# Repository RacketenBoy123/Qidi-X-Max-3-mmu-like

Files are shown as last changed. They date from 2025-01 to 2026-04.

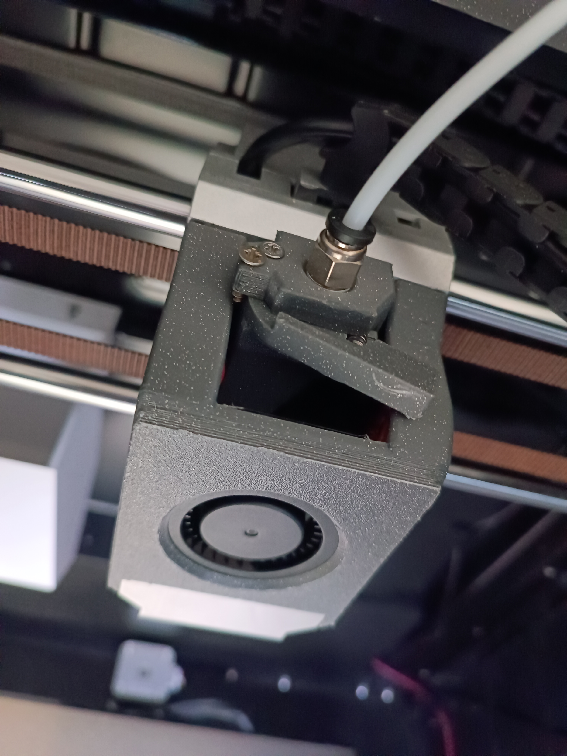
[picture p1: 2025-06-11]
assets/images/Printhead_1.jpg

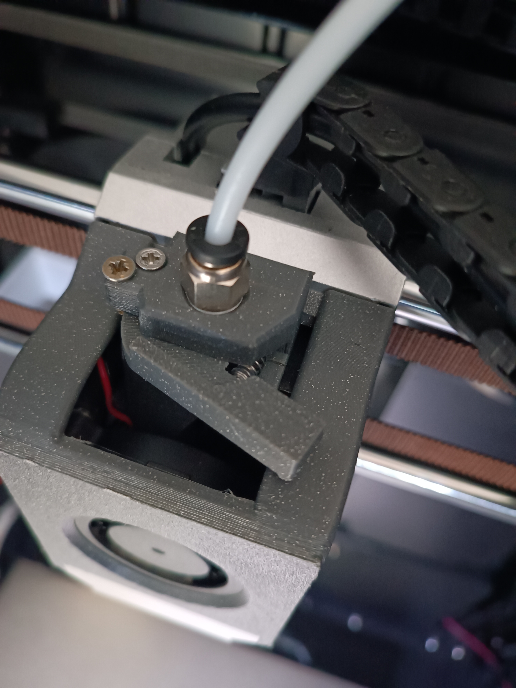
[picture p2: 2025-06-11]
assets/images/Printhead_2.jpg

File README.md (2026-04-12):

# Qidi-X-Max-3 mmu-like BRANCHHHH
 A fan-made MMU/AMS-like system for the Qidi X Max 3
 It is fully created in G-code and uses the FreeDi replacement system for the Qidi printer as a base. For instructions on how to install FreeDi, go here: : [FreeDi](https://github.com/Phil1988/FreeDi/tree/master)

 I also recommend that you upgrade the internal eMMC module to a 32GB one.

# Hardware needed
As of the hardware side you only need:

1. 1 x Bigtreetech SKR Pico
2. 1 to 4 Nema 17 (E series) Motors (Recommended: [Nema 17 Motors](https://www.amazon.de/dp/B0B93PNYCP?ref=ppx_yo2ov_dt_b_fed_asin_title)) and 1 to 4 longer dupont cables 
3. 1 to 4 Extruders with mounting hardware (Recommended: [Dual drive extruder](https://www.amazon.de/dp/B0865SLWQ5?ref=ppx_yo2ov_dt_b_fed_asin_title))
4. PTFE Tubing and fittings (Recommended: [5m PTFE tuning and fittings](https://www.amazon.de/FULARR%C2%AE-Professionell-Teflonrohr-Fitting-Verbinder/dp/B07R9JXQF4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))
5. 16 M3 Heated inserts and 16 M3x7mm screws
6. 1x 5 to 5.5mm diameter spring

Optional:

7. 1 x Ikea Samla 22L box [Link](https://www.ikea.com/de/de/p/samla-box-mit-deckel-transparent-s69440822/#content)
8. Sealing for the Samla box
9. 1 x PVC Pipe, 33mm or 40mm diamater and 32cm length
10. 1 x Hygrometer
11. Silicat

# Disclaimer
Before you print or install anything, be sure to install FreeDi and the matching version of Klipper on your SKR Pico. After that, you can proceed.
A disclaimer before you start: the AMS riser, toolhead, filament cutter, Samla box filament holder, and nozzle wiper are all from different creators. Most of these files I edited and changed to make them work better, but please still support the original creators. All of the original links are in the folders as a text file or in this installation guide. Thanks.
If anthing doesnt work for you or theres a bug in the gcode, please contact me.

# Installation
The first step is printing the needed adapters and hardware. I recommend printing these parts all in either ABS or ASA to make them more heat resistant.
If you don’t know how to proceed at any step, please look at the included pictures or message me. Included pictures are in the /assets/images folder and named after what they might help with assembling. 
Go through the stl_files folder and download the following STL files and print them the amount stated below:

### Ams Riser

1. 1x 4-way_splitter-flat.stl
2. 1x xmax-mmu-lf.stl
3. 1x xmax-mmu-lr.stl
4. 1x xmax-mmu-rf.stl
5. 1x xmax-mmu-rr.stl
6. 8x mmu-xmax_joiner-clip-x8-v1.stl

After printing the needed hardware for the riser, go through the "732980-x-max-3-automatic-multi-material-riser-ec3e07c0-a392-4935-88c6-fceb8f445ebd.pdf" or click this [Link](https://www.printables.com/model/732980-x-max-3-automatic-multi-material-riser/files) to see how to assemble the printed pieces. For that, push the heat-set inserts into the designed holes on the side of the riser pieces with a soldering iron.

### MCU Holder

1. 1x Back_Spool_Holder_Adapter.stl
2. 1x MCU_Holder v2.stl
3. 1x ams_cover.stl (Optional)

Detach the spool holder from the backside of the printer.
Then take the "Back_Spool_Holder_Adapter.stl" and the "MCU_Holder v2.stl" and screw them together. Now place the MCU over the screw holes of the holder, with the heat-set inserts, and screw the SKR Pico onto the holder.
Now place the adapter in the slot that is now free at the back of the printer and slide it down.
Before this step, be sure to power off the printer. Now you just need to open the back plate of the printer, take a USB cable, attach it to the mainboard of the printer, fish it through the vent cutouts, and plug it into the SKR Pico.
After that, make sure to close everything back up, power on the printer, and configure the SKR Pico via SSH [Tutorial](https://www.youtube.com/watch?v=hfD1LAOoBJc).

### Toolhead

This segment contains a replacement for the toolhead cover, to make it more accessible, and a filament cutter that replaces the stock filament guide and adds a place for a knife blade. The STL files also contain a "Cutter_Stop.stl", which is a plug to push into one of the holes in the front of the chassis, which, when equipped with a heat-set insert and a screw, will push the filament cutter in and cut the filament when needed.

1. 1x Cutter_Stop.stl
2. 1x Filament_cutter.stl
3. 1x Filament_cutter_arm.stl

Optional:

4. 1x qidi_front_adapter_short.stl
5. 1x Qidi_front_cover v2.stl
6. You also need magnets with a 10mm daimeter

After printing these parts, unload the filament out of the printhead, power off the printer, and take off the front cover of the toolhead. Take out the original PTFE tube and the original fitting.
Before you now place in the replacement, make sure to screw in one of the fittings (the silver one) into the big hole at the top. I recommend using a bit of heat from a heat gun to preheat the hole so the printed part won’t snap in two.
Now place the "Filament_cutter.stl" onto the printhead; the square pillar should align with the square cutout right beneath the filament inlet.
After that, take the "Filament_cutter_arm.stl", place a small knife blade into the slot on the side, with the hole at one end facing up. After that, take the arm and align the hole at one end with the further back hole of the "Filament_cutter.stl" and put a screw through both of these. Now take the spring and place it on the sideways hole on the "Filament_cutter.stl", the small hole that doesn’t go through and points towards the "Filament_cutter_arm.stl". After that, take another screw and place it in the other hole on the "Filament_cutter.stl" as a stop for the "Filament_cutter_arm.stl" so it doesn’t open too wide.

Printhead_2

At the end put a heat-set insert in the  "Cutter_Stop.stl", put a screw in the insert and let it stick out about 25mm and then push the block in the square hole at the end of the light strip, with the srew further to the top.

Stop_1

After that, you can optionally install the magnetic printhead cover. For that, follow this [Link](https://www.printables.com/model/952804-filament-cutter-for-x-plussmartmax-3-toolhead).

### Poop Bucket

1. 1x Bucket_Filament.stl

Bucket_3

To install this, slide it into the flat steel at the back of the printer (internally) and follow the included pictures.

### Nozzle Wiper

1. 1x Wipe_arm.stl
2. 1x Wipe_clamp.stl

Wiper_1

Follow the included pictures and this [Link](https://www.printables.com/model/722217-qidi-x-max-3-nozzle-scrub-holder)

### Filament Storage

1. 2x Ikea_box_holder.stl
2. 1x to 4x angled_feeder_outside_m6_for_greater_gap.stl

Optional:

3. 2x PVC_Adapter.stl (Optional)
4. 3x Spool Trenner.stl (Optional for 33mm diameter PVC Pipe only)
5. samla_clips.stl (Optional)

Samla_1

Follow this [Link](https://www.thingiverse.com/thing:1752874)

Carto mount: PC
Rest: abs

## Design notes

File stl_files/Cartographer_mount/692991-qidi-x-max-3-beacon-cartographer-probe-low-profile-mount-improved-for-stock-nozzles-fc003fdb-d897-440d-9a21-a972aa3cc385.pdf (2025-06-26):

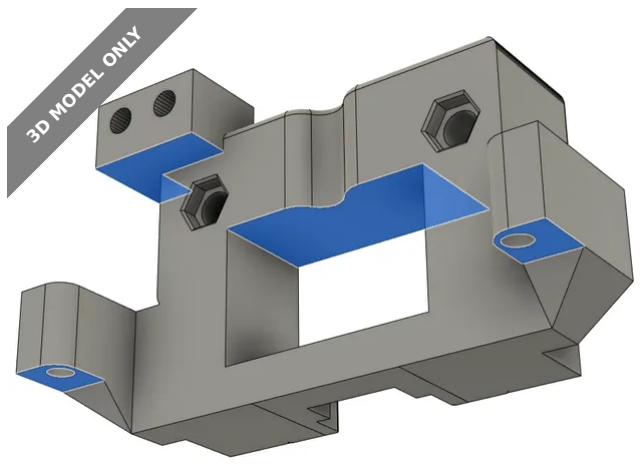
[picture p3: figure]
3D MODEL ONLY

## Summary

QIDI X-Max 3 Beacon / Cartographer low-profile mount for stock nozzle setup

3D Printers (https://printables.com/model?categoryId=1) > Other Printer Parts & Upgrades (https://printables.com/model?categoryId=2)

Tags: | qidi | beacon | qidixmax3 | cartographer

Thnx for @Balgerion for original model!

Update:

Version 2 of mount makes it 1mm lower, for better auto Z calibrations. It does require low-profile button head screws, regular DIN 912 cap head screws won't work. They have too big head

This is slightly improved remix, adding some quality of life features and third leg for stock nozzle setup
If you need X-Plus 3 version, there are some remixes for it
Supported probes:

Mc Sneaky (https://printables.com/@McSneaky_1598019)

## QIDI X-Max 3 Beacon / Cartographer probe (low profile) mount improved for stock nozzles

VIEW IN BROWSER (https://printables.com/model/692991-qidi-x-max-3-beacon-cartographer-probe-low-profile)

updated 23. 11. 2024 | published 23. 11. 2024

This mount works with both Beacon D (https://beacon3d.com/product/beacon/) low profile version and Cartographer (https://cartographer3d.com/) low profile (that's what I'm using)
Needed hardware:
4x M3x14 bolts original stock probe mount bolts. Stock probe has 2 bolts, there should be 2 extra that came with printer / official upgrade package as spare parts
2x M3 nuts to secure probe in place. Those didn't come with printer, had to buy
2x M2.5x16 had those with one of Qidi printers as spare parts too, can't remember if it was iFast or X-Max 3
Optional zipties to secure cable
Print settings:
Print in some high-temp material. PLA will warp most likely, ABS and ASA MIGHT survive. I'd recommend PAHT-CF rated for 190deg C, PP-GF30 or PSU to be sure it doesn't warp nor melt. Did in PAHT-CF myself
I did with 4 walls, 4 top layers, 4 bottom layers, 50% infill
Need supports in two areas marked as blue on model picture After-installation needed config changes Cartographer:

Install Carto in Klipper: Carto install docs (https://docs.cartographer3d.com/installation-and-setup/klipper-setup)

Modify printer.conf

Comment out / remove whole [homing_override] section
Under [bed_mesh]
mesh_min:25,25 # this needs to be set to 25,25 from stock 25,15 speed:500 # increase speed for faster scanning, can leave stock probe_count:30,30 # increase points count, can leave stock
Add [cartographer] and [safe_z_home] sections following to their doc (https://docs.cartographer3d.com/installation-and-setup/klipper-config)
under [cartographer] need to set y_offset: 25
under [safe_z_home] need to set home_xy_position: 162.5, 162.5
Remove / comment out any [probe] and [bltouch] sections Follow Carto docs (https://docs.cartographer3d.com/installation-and-setup/cartographer-calibration) for initial calibration. It's super easy, just 2-3 steps

Running full bed mesh at 300mm/s. Printer should also be able to handle 600mm/s

Beacon:
- Don't know. Ask @Balgerion =)

## This remix is based on

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
## Model files

QIDI X Smart/Plus/Max Beacon probe (low profile) mount (https://printables.com/model/639766-qidi-x-smartplusmax-beacon-probe-low-profile-mount)
by Balgerion (https://printables.com/@Balgerion_812626)

## License

This work is licensed under a GNU

General Public License v2.0 (http://www.gnu.org/licenses/old-licenses/gpl-2.0.html)

✖ | Sharing without ATTRIBUTION
✔ | Remix Culture allowed
✔ | Commercial Use
✔ | Meets Open Definition

qidi_beacon_mount.stl

qidi_beacon_mount.obj

qidi_beacon_mount.step

beacon_carto_mount_v2.stp

beacon_carto_mount_v2.stl ℹ | Share under the same license

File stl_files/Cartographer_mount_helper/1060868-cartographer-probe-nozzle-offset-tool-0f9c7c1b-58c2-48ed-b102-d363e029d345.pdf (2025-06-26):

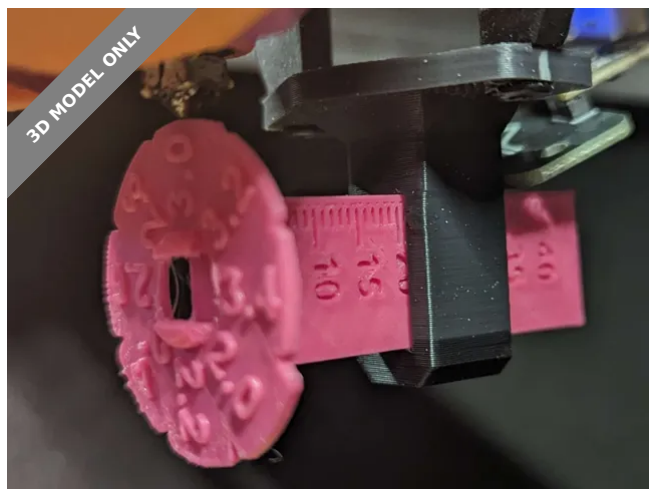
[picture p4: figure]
3D MODEL ONLY

## Summary

A simple tool to help find the Z and Y offset for your Cartographer probe.

3D Printers (https://printables.com/model?categoryId=1) > Other Printer Parts & Upgrades (https://printables.com/model?categoryId=2)

Tags: cartographer

This simple tool helps find the proper offset for your Cartographer probe in relation to your nozzle tip.
Having a 2.6-3mm Z offset is critical for reliable operation of Cartographer Touch (nozzle probling).
The Y offset ruler is just a helpful addition.
To use, simply print the parts (they are already in proper printing orientation in the .3mf file) and then clip the “flower” onto the “ruler” then slide the “ruler” into the base.
Then simply remove your cartographer from your mount and replace it with the tool. Slide the ruler until the flower is underneath the nozzle, then rotate the flower until one of the faces is touching the nozzle.
The numbers on the flower indicate your Z offset, and the ruler mark that lines up with the base indicates your Y offset (you can also use calipers to measure from the back face of the flower to the front face of the base and this will also be your Y offset).

E (https://printables.com/@Esoterical_306854) Esoterical (https://printables.com/@Esoterical_306854)

## Cartographer probe nozzle offset tool

VIEW IN BROWSER (https://printables.com/model/1060868-cartographer-probe-nozzle-offset-tool)

updated 20. 11. 2024 | published 20. 11. 2024

## Model files

## License

This work is licensed under a GNU

General Public License v3.0 (https://www.gnu.org/licenses/gpl-3.0.html)

✖ | Sharing without ATTRIBUTION
✔ | Remix Culture allowed
✔ | Commercial Use
✔ | Meets Open Definition
ℹ | Share under the same license carto_nozzle_offset_tool.3mf

carto_nozzle_offset_tool.step

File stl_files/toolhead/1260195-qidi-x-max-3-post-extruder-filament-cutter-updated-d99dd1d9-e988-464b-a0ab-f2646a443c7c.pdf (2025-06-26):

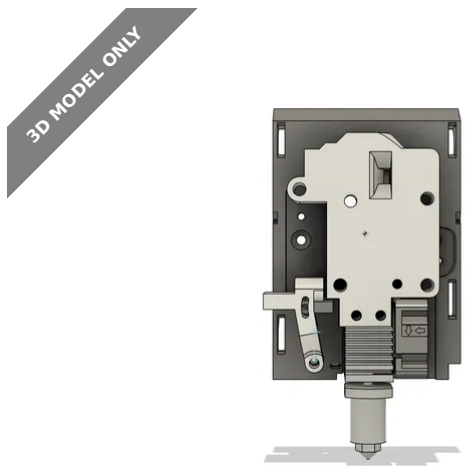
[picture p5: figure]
3D MODEL ONLY

## Summary

QIDI X-Max 3 extruder with ECAS fitting and runout sensor and extruder disengage slot.

3D Printers (https://printables.com/model?categoryId=1) > Other Printer Parts & Upgrades (https://printables.com/model?categoryId=2)

Tags: | extruder | filamentcutter | qidi | qidixmax3

I believe I have a working Beta

Updated: (4/22/2025)

https://vimeo.com/manage/videos/1077693101/502d7b66e4

This is a work in progress! Proceed with caution.

Additionally, this will also require a new homing procedure.

The goal of this project is to add a sturdy and integrated filament cutter that minimizes waste while keeping the rest of the printer as stock as possible.

AskewedBox (https://printables.com/@AskewedBox_2060075)

## QIDI X-Max 3 (Post Extruder) Filament cutter (Updated)

VIEW IN BROWSER (https://printables.com/model/1260195-qidi-x-max-3-post-extruder-filament-cutter-updated)

updated 22. 4. 2025 | published 22. 4. 2025

This design is a modified version of the original extruder body. It includes a filament cutter "blade port" positioned directly above the hotend and has been simplified for easier printing.

Side note: QIDI originally had a design for this but not on the release model I have.

In addition to the filament cutter, this modification incorporates a filament runout sensor placed above the extruder. The runout sensor utilizes a 5 mm bearing (original this was a 4.5mm BB) and an Omron D2F style limit switch: https://www.digikey.com/en/products/detail/omron-electronics-inc-emc-div/D2F/83270 (https://www.digikey.com/en/products/detail/omron-electronics-inc-emc-div/D2F/83270)
Required:

Printed Parts

Extruder Cover (Front (no supports needed), Left Panel, Right Panel) Lever Arm
Lever Arm Spacer
Blade Holder (print a few)
Notes
I printed in ABS with 40% infill and 4 walls.
The Left and Right Panels as well as the lever arm need support everything else should be fine.
I was having issues with the tabs snapping no matter how I printed them so I broke it up into multiple parts them printed for strength. As a plus this makes it easier to transfer the extruder fan.

Filament Sensor

1x 5mm Bearing
1x Omron D2F style limit switch
2x Self-tapping M2x8mm screws
Optional but helpful: long M2 screws to adjust the limit switch

Extruder

ECAS04
4x M3 heat set inserts of any length for the extruder body
2x M3x4 heat set inserts for the hotend mount holes
2x M3 heat set inserts of any length for the cover if you print this in multiple pieces.

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
Cutter

18mm Snap-off Blade with 8mm segments - I bought mine at Harbor Freight.
1x M3X20 screw
4 mm OD, 0.5mm Wire Size, 15 mm compression spring - It is important that these are stiff, I got mine from my Box Turtle Kit These should work but are untested https://www.amazon.com/gp/product/B0C33BYX83/ (https://www.amazon.com/gp/product/B0C33BYX83/)
Superglue
Instructions (in work):

Extruder

Insert the ECAS fitting (this should be hard to insert, I pressed it in using a vise)
Filament Sensor
Insert the 5mm bearing ensuring that it moves freely.
Insert the limit switch in the correct orientation
Insert the optional M2 screws to apply pressure light pressure to the switch.
To adjust the placement of the switch take a piece of filament and insert it in the extruder listening for a click as you insert it. If you don't hear a click tighten the M2 screws and try again.
It is critical that you ensure that the switch is triggered by the filament before setting its placement permanently. Use the Self-tapping M2 screws set the switch location. Transfer the extruder hardware from the stock extruder. Be careful not to lose the tension spring or the gear bearings. The print is designed without tolerances for the bearings or gear pins, so some hardware mainly the dowel pins, may be difficult to insert.
I pressed in the bearing and reamed the dowel hole with a 3mm bit.
This will still be tight fit but easer to remove if needed. Insert 4 M3 heat-set inserts into the extruder body flush.
For the hotend, ensure the inserts are 4mm or less. Reassemble the extruders gears and reattach the back plate Check that the gears turn freely
Notes
Don't attach the hotend yet; you will want it off to verify blade length and smooth movement.
Ensure that no plastic is displaced that will cause the blade to bind.

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
The have been increased to 4.2 mm but might still be slightly undersized
Ensure the tenson spring is not binding on the plastic was displaced by the insert.

Blade Holder

-----Use Caution when handling and snaping the blades!

The holder is designed for a 8mm wide section from a snap-off box cutter blade
The blade needs to be snapped to a length of of approximately ~18mm (measures from the cutting edge) or slightly less. Insert the blade into the holder such that the lever assembly is around 25.7mm (This is what worked for me through guess and check)
Glue the blade into the holder.
Now is a good time to check that the blade is free moving in the extruder blade slot and that it extends past the filament hole by at least 1mm.
Note
I used a vise and pliers to snap this to make clean(er) breaks but even then it wasn't consistent.
The goal is to have a blade length that is long enough to cut the filament but isn't so long that it binds when retracted by the spring.
It is hard to snap this exactly and this might take a few tries.
This section will probably require trial and error.
The lever arm length and hole depth were fiddly to get just right and may require adjusting to get the correct blade length.

Lever Arm

Screw the assembled holder into the lever with two short M2 screws, Don't over tighten these since they should be free moving. Insert the M3x20 mm screw into the lever arm (these should be relatively free moving on the screw.
Insert the screw into the printed spacer.
Screw the lever are onto the preexisting hole with a threaded insert next to the hotend

____________________________________________

Untested Best Guess at Hotend Values BoxTurtle MMU:

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
## Model files

tool_stn: 44.5
tool_stn_unload: 96.6
variable_retract_length: 23.7 variable_pushback_length: .9 (most likely wrong)

## This remix is based on

GitHub - vega-d/qidi_mods: a set of mods to qidi printers. Assorted by model. (https://github.com/vega-d/qidi_mods)

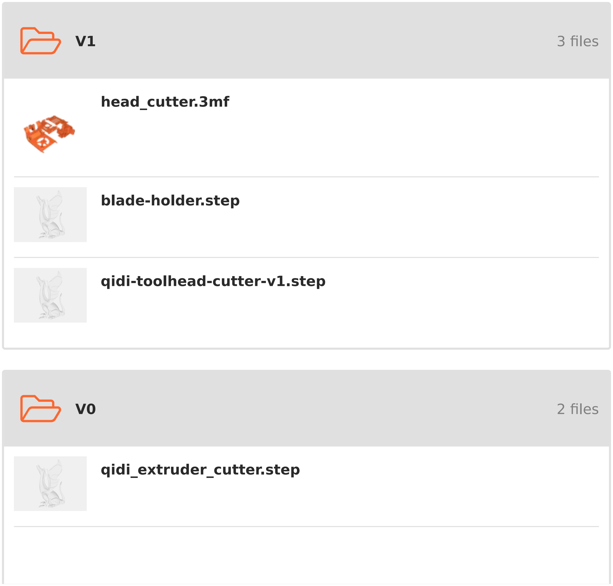
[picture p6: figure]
3 files; 2 files; head_cutter.3mf; blade-holder.step; qidi-toolhead-cutter-v1.step; qidi_extruder_cutter.step

## License

This work is licensed under a
Creative Commons (4.0 International License)

Attribution (http://creativecommons.org/licenses/by/4.0/)

✖ | Sharing without ATTRIBUTION
✔ | Remix Culture allowed
✔ | Commercial Use
✔ | Free Cultural Works
✔ | Meets Open Definition

qidi_extruder_assembly.step

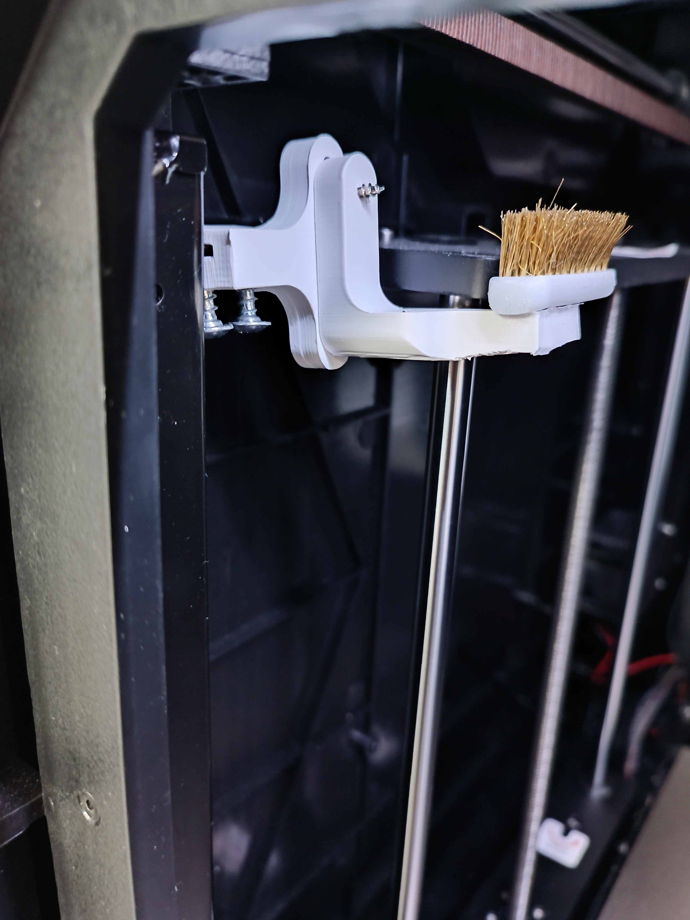
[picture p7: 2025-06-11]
assets/images/Wiper_1.jpg

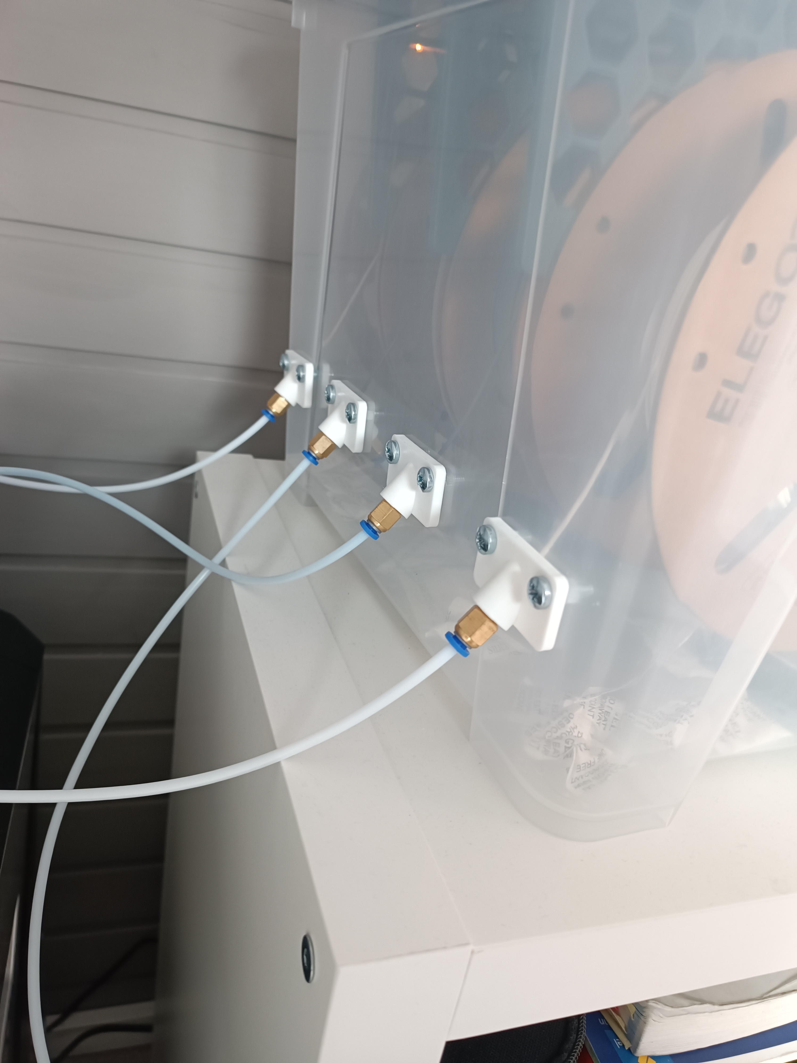
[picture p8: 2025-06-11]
assets/images/Samla_1.jpg

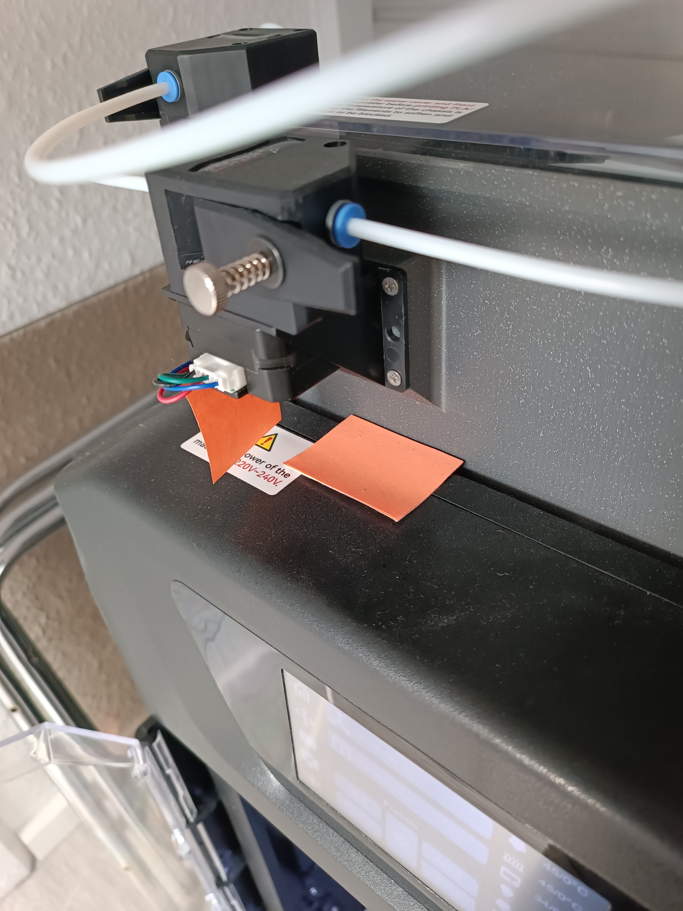
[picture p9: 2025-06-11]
assets/images/Riser_2.jpg

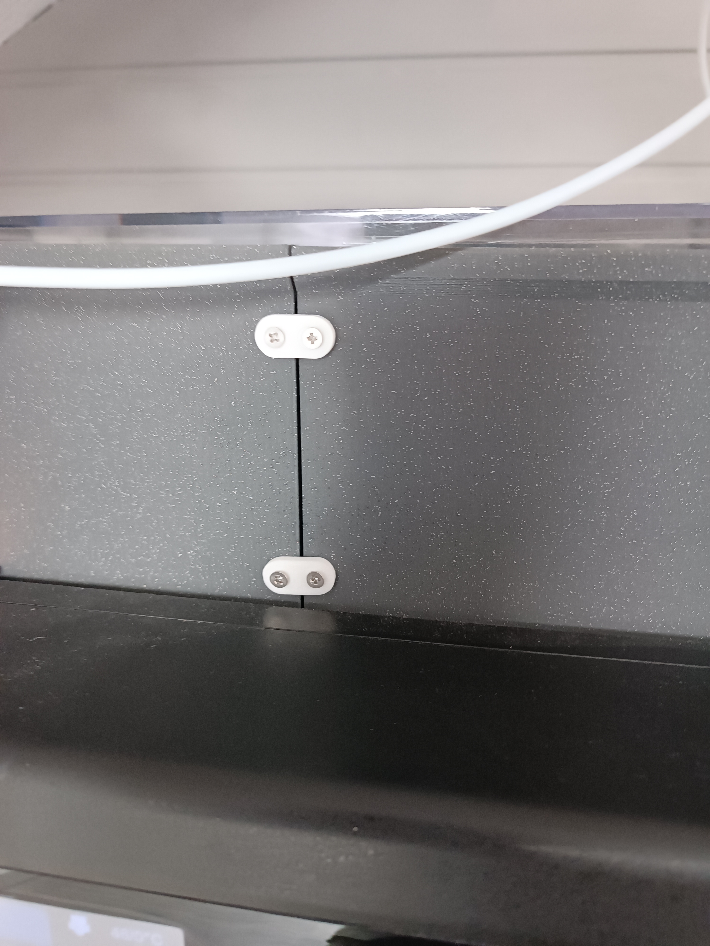
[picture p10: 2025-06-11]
assets/images/Riser_3.jpg

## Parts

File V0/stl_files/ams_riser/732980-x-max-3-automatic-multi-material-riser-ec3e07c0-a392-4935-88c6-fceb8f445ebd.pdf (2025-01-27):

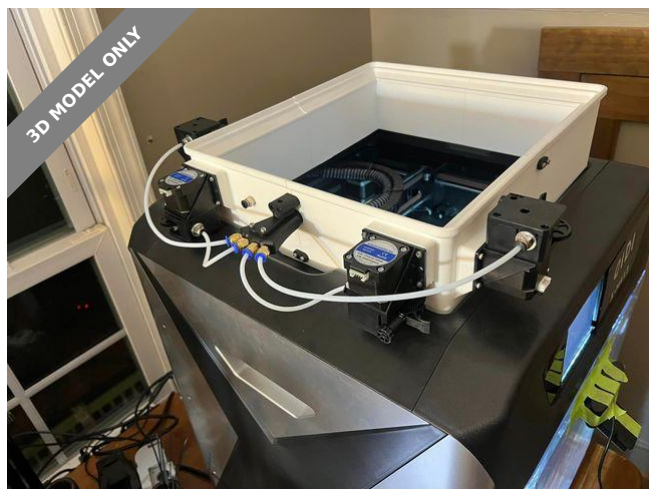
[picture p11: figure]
3D MODEL ONLY

## Summary

Multi material and color

3D Printers (https://printables.com/model?categoryId=1) > Other Printer Parts & Upgrades (https://printables.com/model?categoryId=2)

Tags: mmu | qidi | ams | xmax3

this is for the qidi x max 3.

its a riser in 4 pieces meant to house a splitter a pc4 m10 coupler and up to 8 titan extruders acting as feeder extruders to be synced with your DD extruder.

you will need either a board upgrade with more stepper drivers or an expansion board. im using a BTT Octopus v1.1

i use the Jazz3D Spit Fire print head with the filament cutter to make color/ material changes seemless. which uses the orbiter v2 and a rapido uhf.

recommend printing in petg or abs very minimal support roughly 1.5kg in filament depending on your print settings.

i provided the dxf if youd like to get a poly carbonate top made

you will need pc4 6mm couplings and drill the brass out with 4mm drill bit for smooth transition to the splitter and the pc4 10mm once Bowden is

z (https://printables.com/@zfriedman302_262860) zfriedman302 (https://printables.com/@zfriedman302_262860)

## X Max 3 Automatic

## Multi Material Riser

VIEW IN BROWSER (https://printables.com/model/732980-x-max-3-automatic-multi-material-riser)

updated 3. 3. 2024 | published 3. 3. 2024

## Model files

pushed thru you need to flare the ptfe I used a drill with a #2 Phillips and flared it

mmu-xmax_joiner-clip-x8-v1.stl

xmax-mmu-lr.stl

mmu-xmax_splitter-bracket-v1.stl

xmax-mmu-lf.stl

xmax-mmu-rf.stl

xmax-mmu-rr.stl

4-way_splitter-flat.stl

3-way_splitter-flat.stl

## License

This work is licensed under a
Creative Commons (4.0 International License)

Attribution-NonCommercial (http://creativecommons.org/licenses/by-nc/4.0/)

✖ | Sharing without ATTRIBUTION
✔ | Remix Culture allowed
✖ | Commercial Use
✖ | Free Cultural Works
✖ | Meets Open Definition

2-way_splitter.stl

xmax-3-lid.dxf

mmu-xmax-v21.f3d

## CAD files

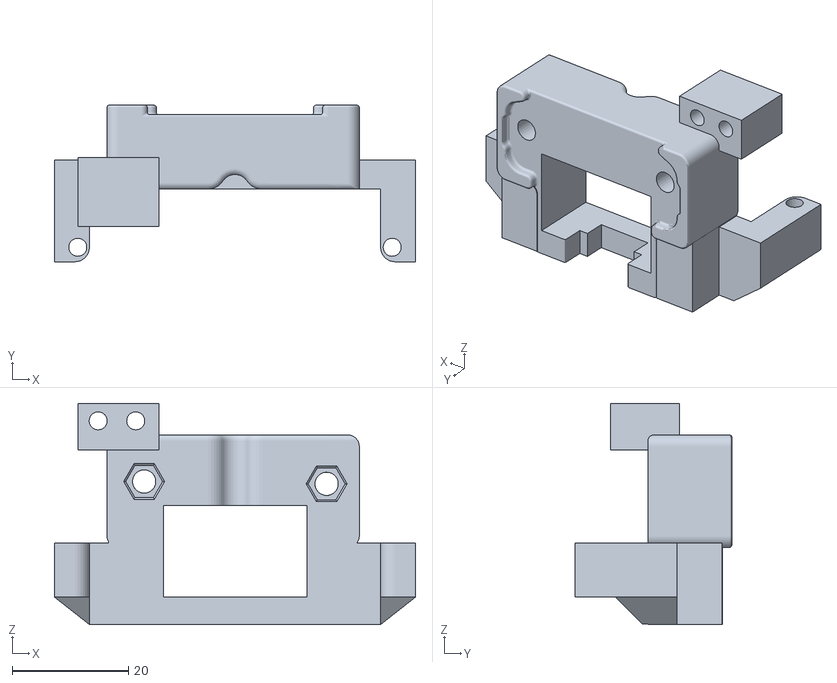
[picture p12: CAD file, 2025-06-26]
stl_files/Cartographer_mount/beacon_carto_mount_v2.stl
62.0 x 26.9 x 38.0

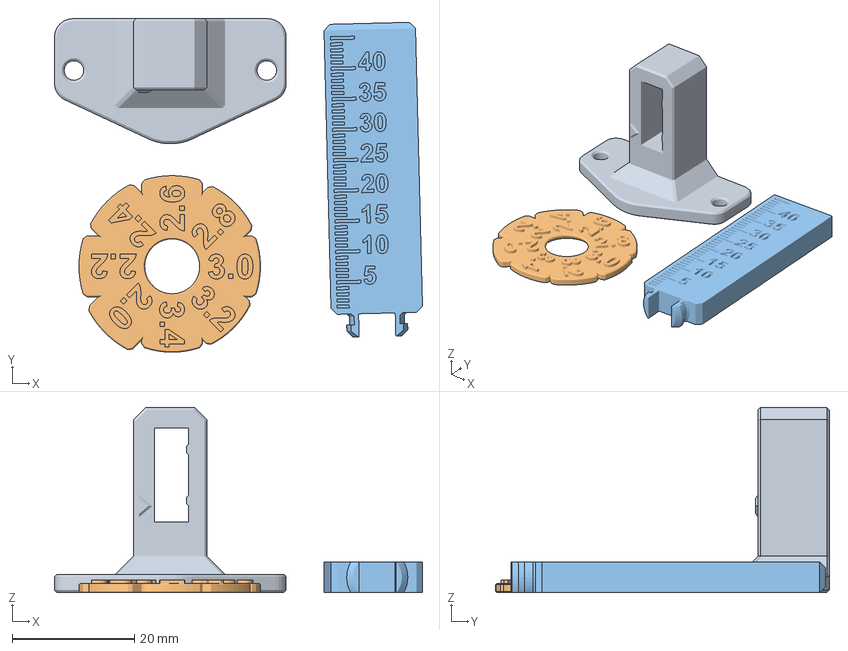
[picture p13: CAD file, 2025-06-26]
stl_files/Cartographer_mount_helper/carto_nozzle_offset_tool.3mf
60.3 x 54.6 x 30.3 mm

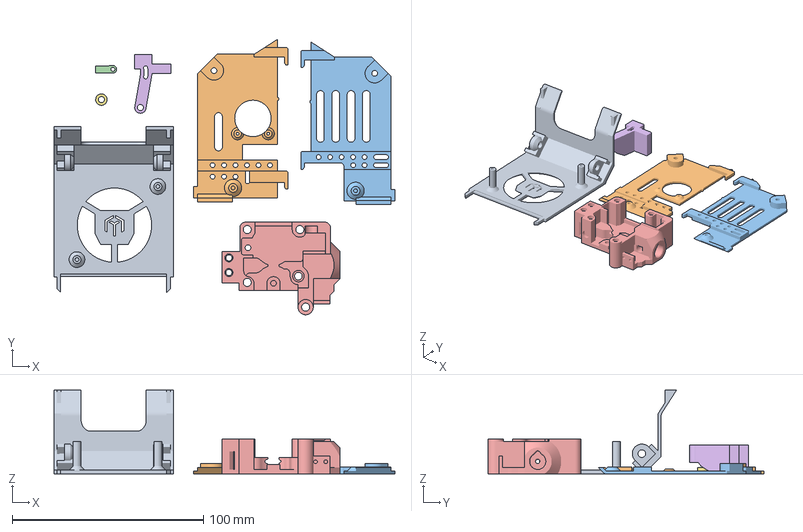
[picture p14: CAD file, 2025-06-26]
stl_files/toolhead/head_cutter.3mf
178.2 x 144.0 x 43.9 mm
Front Cover
Left
Right
Lever
Spacer

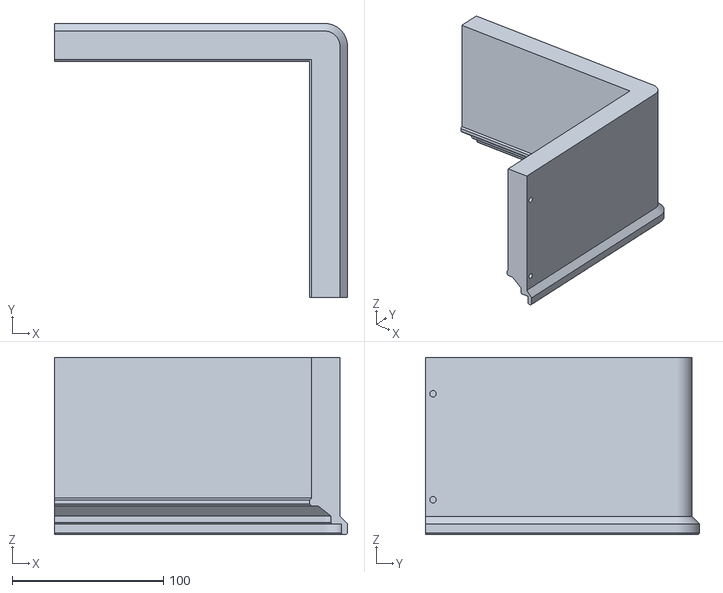
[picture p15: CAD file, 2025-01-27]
V0/stl_files/ams_riser/xmax-mmu-lf.stl
193.5 x 181.0 x 117.0

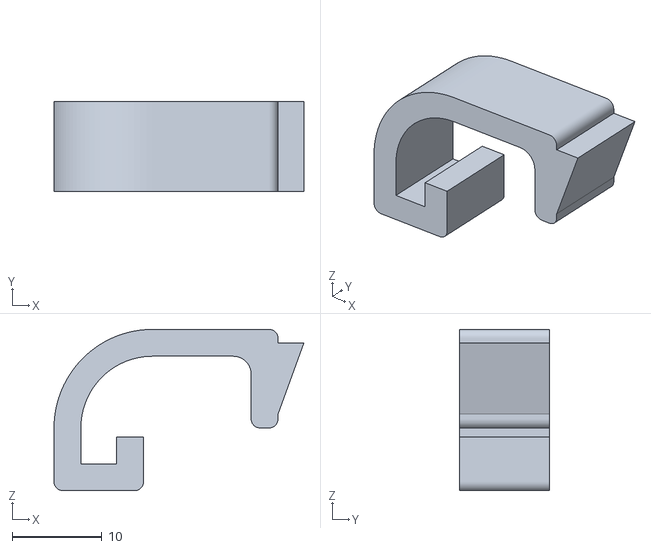
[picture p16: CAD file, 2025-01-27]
V0/stl_files/ikea_samla/samla_clips.stl
27.9 x 10.0 x 18.0

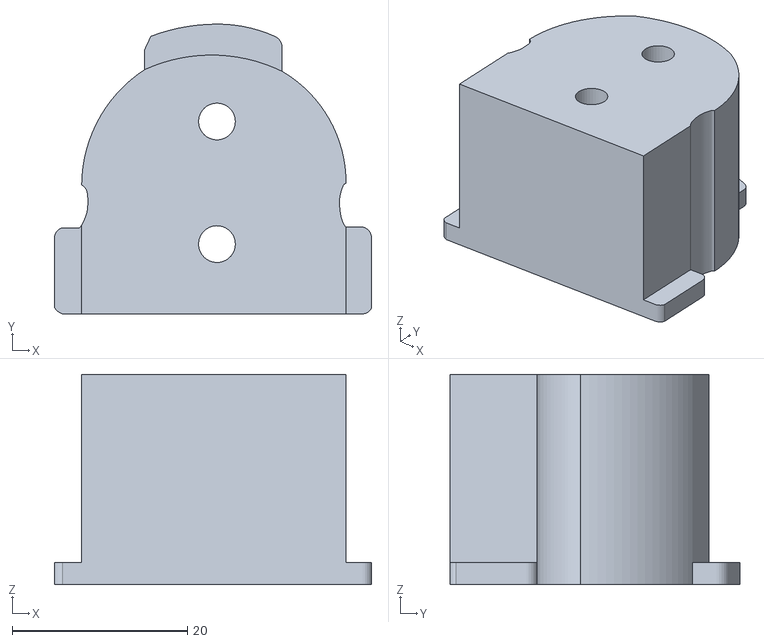
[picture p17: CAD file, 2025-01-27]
V0/stl_files/mcu_holder_and_cover/Back_Spool_Holder_Adapter.stl
36.2 x 33.1 x 24.0

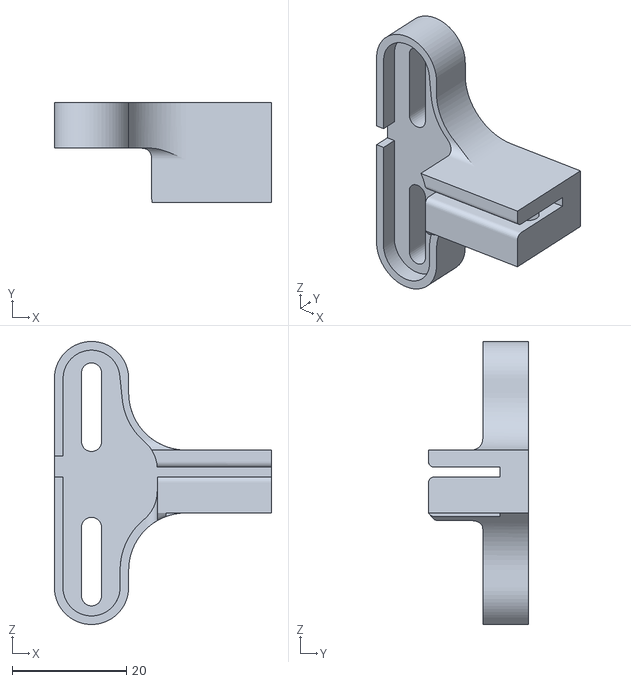
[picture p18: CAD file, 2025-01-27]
V0/stl_files/nozzle_wiper/Wipe_clamp.stl
38.0 x 17.5 x 49.5

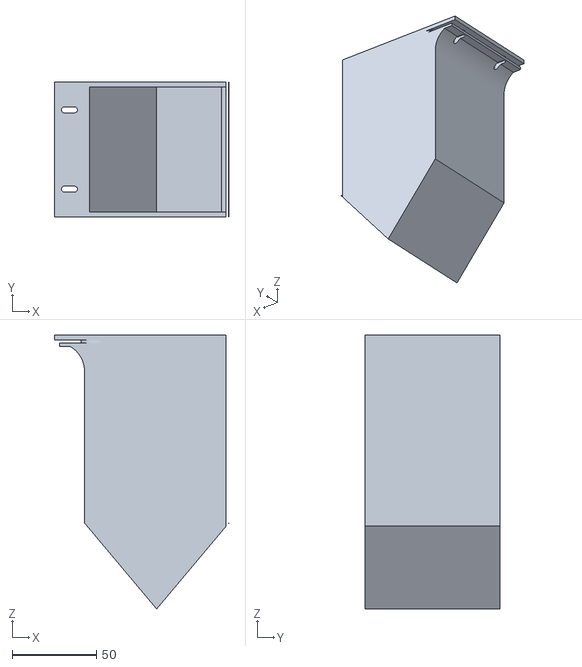
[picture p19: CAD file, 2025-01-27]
V0/stl_files/poop_bucket/Bucket_Filament.stl
103.5 x 80.0 x 162.6

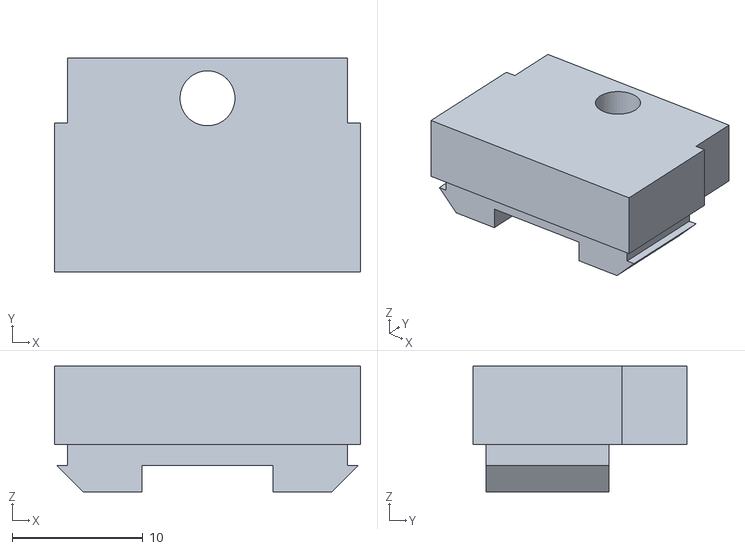
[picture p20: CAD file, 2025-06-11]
V0/stl_files/toolhead/Cutter_Stop.stl
23.4 x 16.4 x 9.60

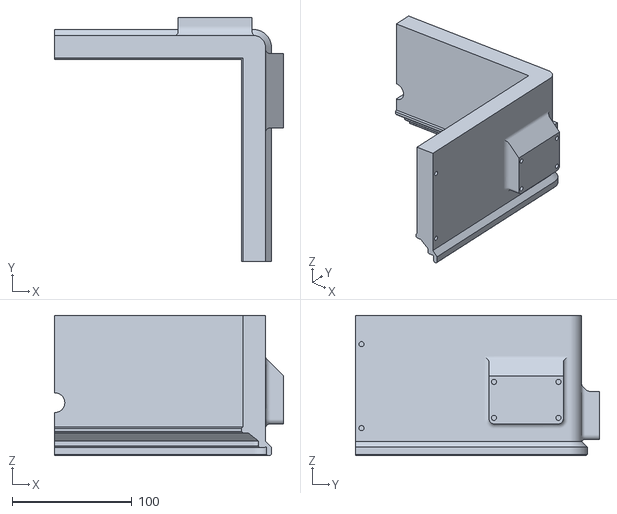
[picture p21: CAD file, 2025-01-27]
V0/stl_files/ams_riser/xmax-mmu-rf.stl
191.0 x 203.5 x 117.0

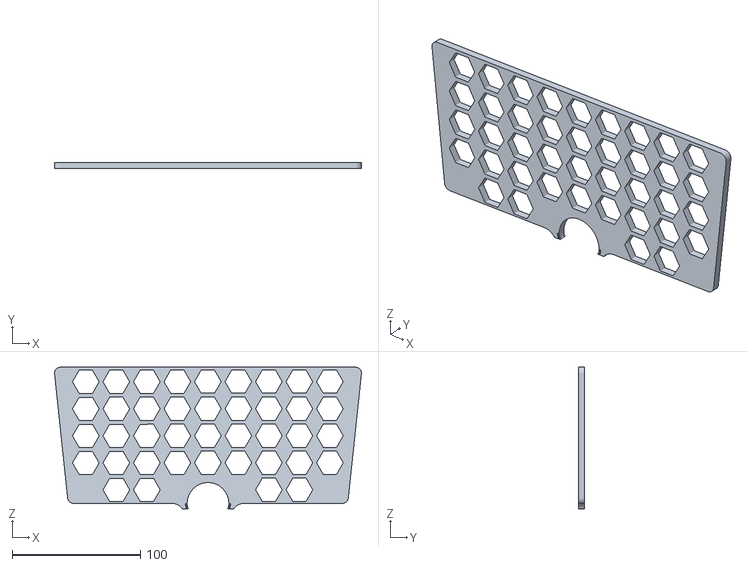
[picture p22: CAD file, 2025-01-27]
V0/stl_files/ikea_samla/Spool Trenner.stl
239.0 x 5.00 x 110.3

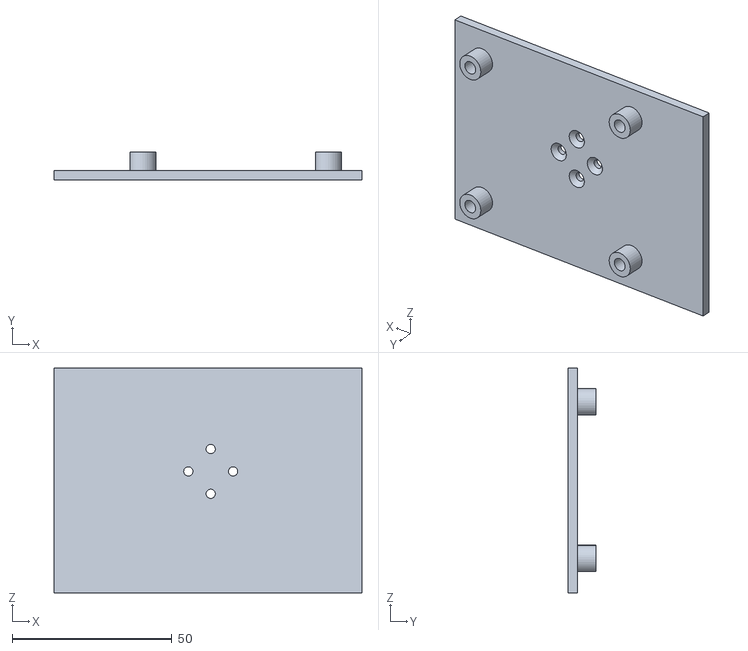
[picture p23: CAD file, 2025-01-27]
V0/stl_files/mcu_holder_and_cover/MCU_Holder v2.stl
96.3 x 8.80 x 70.3

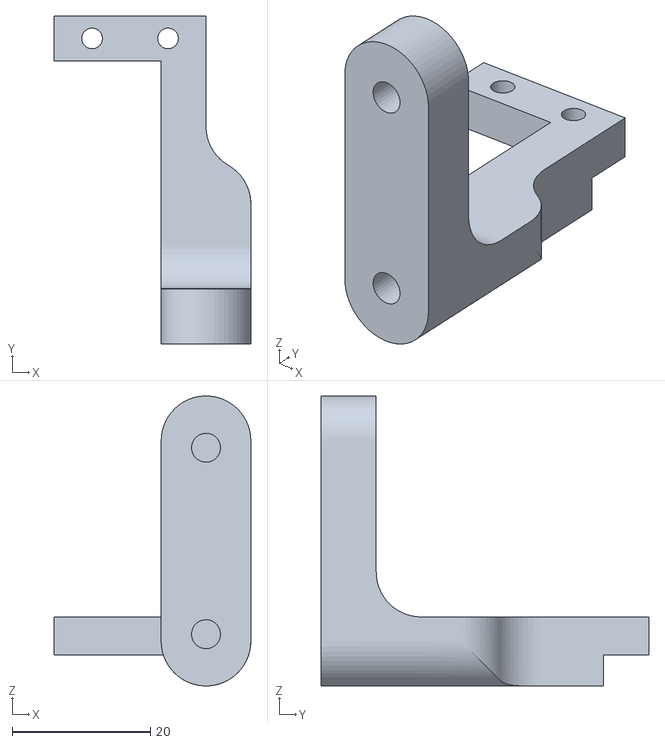
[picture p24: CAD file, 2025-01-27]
V0/stl_files/nozzle_wiper/Wipe_arm.stl
28.5 x 47.5 x 42.0

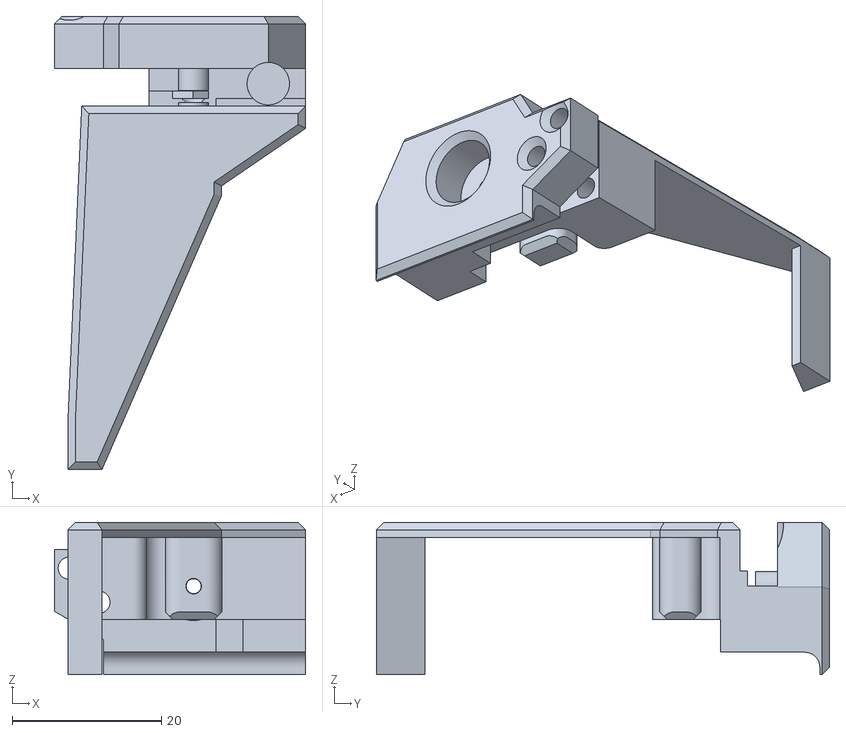
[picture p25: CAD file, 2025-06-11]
V0/stl_files/toolhead/Filament_cutter.stl
33.7 x 60.7 x 20.4

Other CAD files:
V0/stl_files/ams_riser/xmax-mmu-lr.stl
V0/stl_files/ikea_samla/PVC_Adapter.stl
V0/stl_files/mcu_holder_and_cover/ams_cover.stl
V0/stl_files/toolhead/qidi_front_adapter_short.stl
V0/stl_files/ams_riser/mmu-xmax_joiner-clip-x8-v1.stl
V0/stl_files/ams_riser/mmu-xmax_splitter-bracket-v1.stl
V0/stl_files/ams_riser/xmax-mmu-rr.stl
V0/stl_files/ikea_samla/Ikea_box_holder.stl
V0/stl_files/ikea_samla/angled_feeder_outside_m6_for_greater_gap.stl
V0/stl_files/toolhead/Filament_cutter_arm.stl
V0/stl_files/toolhead/Qidi_front_cover v2.stl

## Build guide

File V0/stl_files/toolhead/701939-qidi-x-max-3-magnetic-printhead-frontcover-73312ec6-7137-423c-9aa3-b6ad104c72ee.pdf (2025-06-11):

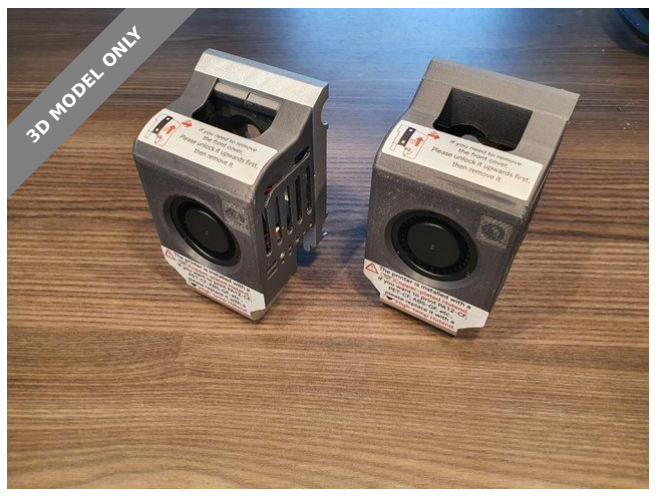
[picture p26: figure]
3D MODEL ONLY

## Summary

Magnetic frontcover for X-Max3 for original base plate with adapter and version with new base plate.

3D Printers (https://printables.com/model?categoryId=1) > Other Printer Parts & Upgrades (https://printables.com/model?categoryId=2)

Tags: qidi | qidixmax | xmax3

Designed a magnetic frontcover for the printhead, that can be used with the original Printhead without further modification (adapter required) and a version with a new base plate.

I keep the original style and dimensions as good as possible.

For this design you will need eight magnets in size: diameter = 6mm , height =3mm.

For example: https://www.amazon.de/UTOMAG-Multi-Use-Neodym-Magnete-Aufbewahrungs/dp/B08F7HNG45?th=1 (https://www.amazon.de/UTOMAG-Multi-Use-Neodym-Magnete-Aufbewahrungs/dp/B08F7HNG45?th=1)

For the new base plate you will need four M3 heatinserts. I used “ruthex M3 Gewindeeinsatz – RX-M3x5.7”, but you can use also shorter ones.

Getfar (https://printables.com/@Getfar_1603461)

## QIDI X-Max 3

## Magnetic Printhead-Frontcover

VIEW IN BROWSER (https://printables.com/model/701939-qidi-x-max-3-magnetic-printhead-frontcover)

updated 23. 1. 2024 | published 23. 1. 2024

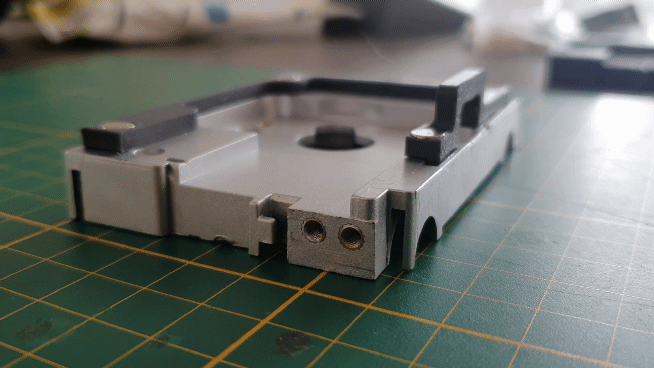
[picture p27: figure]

Changelog:

Added versions with logos

Printinstruction:

Printed the cover laying flat on the big fan hole with 0,12mm layer height, 4 perimeter, supports, brim, 30% infill with ASA.

Printed the base plate laying flat on biggest surface with 0,12mm layer height, 4 perimeter, supports, brim, 30% infill with ASA.

Printed the adapter splitted in the middle and added a connection pin and printed it standing up. This print orientation should be the strongest for the small hooks. Printed in 0,2mm layer height, 6 perimeter, supports, (brim), 100% infill with ASA.

Postprocessing:

For the magnets pay attention for the orientation, so that that the magnets attach correctly to eachother. All magnets are glued to the holes.

For good fit its crucial to remove all supports with care and deburre alle edges (especial the elephante footprints)

Its also benefical to srcew in all bolts before assembly, so that all threads are cut. (I heated the bolts before installation).

For the base plate its required to insert M3 heatinserts with a soldering iron.

•

## Model files

For switching the original fans and duct. Install first the lower bolt of the cable clamp for the fan duct, than install the fan duct and last the small fan with cable clamp.

## License

This work is licensed under a
Creative Commons (4.0 International License) (http://creativecommons.org/licenses/by-nc-sa/4.0/)

qidi_front_full.stl

qidi_front_full_logo.stl

qidi_base_full.stl

qidi_front_adapter_short.stl

qidi_front_short.stl

qidi_front_short_logo.stl

Attribution—Noncommercial—Share Alike (http://creativecommons.org/licenses/by-nc-sa/4.0/)

✖ | Sharing without ATTRIBUTION
✔ | Remix Culture allowed
✖ | Commercial Use
✖ | Free Cultural Works
✖ | Meets Open Definition

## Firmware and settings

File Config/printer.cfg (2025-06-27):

# X-MAX3 config created by Phil1988(github)/coco.33(discord) on 01.09.2024
# If you want to compile a klipper firmware ("make menuconfig") choose:
# Processor model: stm32f407 
# Bootloader offset: 32KiB bootloader
# Communication interface: (Serial) ( on USART1 PA10/PA9))

# Copy the generated "out/klipper.bin" file to a SD card and rename it to: X_4.bin
# Insert the SD cart to the mainboards sd slot.
# Poweroff and restart the printer to flash the mainboard mcu.
# Poweroff and remove SD cart to the mainboards sd slot.


#####################################################################
# Freedi
#####################################################################
[freedi]
# Printer model. Currently supported: x-smart3, x-plus3, x-max3, q1-pro, plus4
printer_model: x-max3
# Baud rate for serial communication. Stock mainboard with standard firmware: 921600 | Legacy firmware: 115200
baudrate: 921600
# Serial port for the LCD. Stock: /dev/ttyS1 | USB<->TTL adapter: /dev/ttyUSB0 | BTT Manta M5P: /dev/ttyS0
serial_port: /dev/ttyS1
# URL of the printer service
url: 127.0.0.1
# API key for the printer
api_key: XXXXXX
# Path to the Klippy socket file
klippy_socket: /home/mks/printer_data/comms/klippy.sock
# Specify if you want to use the stable or beta channel. Caution: beta firmwares have more potential to have bugs.
channel: stable

#####################################################################
# Kinematics
#####################################################################
[printer]
kinematics:corexy
max_velocity: 600
max_accel: 20000
max_z_velocity: 20
max_z_accel: 500
square_corner_velocity: 8

#####################################################################
# Motherboard and periphery
#####################################################################
[temperature_sensor Mainboard_RK3328]
sensor_type: temperature_host
min_temp: 10
max_temp: 100

[mcu]
serial: /dev/ttyS0
restart_method: command

[temperature_sensor Mainboard_STM32F407]
sensor_type: temperature_mcu
sensor_mcu: mcu

[mcu MKS_THR]
serial: /dev/serial/by-id/usb-Klipper_rp2040_959B8B1663B54E58-if00

[temperature_sensor Toolhead_RP2040]
sensor_type: temperature_mcu
sensor_mcu: MKS_THR
min_temp: 0
max_temp: 100


#####################################################################
# Features
#####################################################################
# For saving GCODE files
[virtual_sdcard]
path: ~/printer_data/gcodes
on_error_gcode: 
  CANCEL_PRINT
  M104 S0          # Turn off extruder
  M140 S0          # Turn off bed
  M106 S0          # Turn off fans

# For enabling pause/resume
[pause_resume]

# Activating exclude objects feature
[display_status]
[exclude_object]

# Expanding idle timeout
[idle_timeout]
timeout: 5400   ; 90min timeout

# Activating GCODE arc feature
[gcode_arcs]
resolution: 1.0

# Allowing free move (can be dangerous!)
[force_move]
enable_force_move: True


#####################################################################
# Macros
#####################################################################
[include macros.cfg]
[include Ams_macro_V2.cfg]
[include Ams_v2.cfg]


#####################################################################
# Input shaping
#####################################################################
[resonance_tester]
accel_chip:adxl345
probe_points:
    160, 160, 10  # an example
    
[adxl345]
cs_pin: MKS_THR:gpio13
spi_software_sclk_pin: MKS_THR:gpio14
spi_software_mosi_pin: MKS_THR:gpio15
spi_software_miso_pin: MKS_THR:gpio12
axes_map: -x, z, -y

[input_shaper]
#shaper_type_x: ei
#shaper_freq_x: 53.4
#shaper_type_y: zv
#shaper_freq_y: 41.4

#####################################################################
# Hotend
#####################################################################
[extruder]
step_pin: MKS_THR:gpio5
dir_pin: MKS_THR:gpio4
enable_pin: !MKS_THR:gpio10
rotation_distance: 53.5
gear_ratio: 1628:170				
microsteps: 16
full_steps_per_rotation: 200
nozzle_diameter: 0.400
filament_diameter: 1.75
min_temp: 0
max_temp: 360
min_extrude_temp: 170
smooth_time: 0.000001
step_pulse_duration:0.000002

heater_pin: MKS_THR:gpio0
sensor_type:MAX6675
sensor_pin:MKS_THR:gpio17
max_power: 1.0
control: pid  
# pid_Kp: 32.468
# pid_Ki: 14.430
# pid_Kd: 18.263
pid_Kp: 14.734
pid_Ki: 6.549 
pid_Kd: 8.288

spi_speed: 100000
spi_software_sclk_pin:MKS_THR:gpio18
spi_software_mosi_pin:MKS_THR:gpio19
spi_software_miso_pin:MKS_THR:gpio16

pressure_advance: 0.020
pressure_advance_smooth_time: 0.03
max_extrude_cross_section:500
instantaneous_corner_velocity: 10.000
max_extrude_only_distance: 1000.0
max_extrude_only_velocity:5000
max_extrude_only_accel:2000

[verify_heater extruder]
max_error: 120
check_gain_time:20
hysteresis: 5
heating_gain: 1


#####################################################################
# Heated bed
#####################################################################
[heater_bed]
heater_pin:PC8
sensor_type: NTC 100K MGB18-104F39050L32
sensor_pin: PA0
max_power: 1.0
control: pid
pid_kp: 70.304
pid_ki: 0.514
pid_kd: 2401.758
# pid_kp: 64.431
# pid_ki: 2.845
# pid_kd: 364.839
min_temp: -50
max_temp: 125

[verify_heater heater_bed]
max_error: 200
check_gain_time:60
hysteresis: 5
heating_gain: 1

#####################################################################
# Bed mesh
#####################################################################
[bed_mesh]
speed:150               
horizontal_move_z: 10 
mesh_min:25,8        
mesh_max:305,305     
probe_count:9,9     
algorithm:bicubic
bicubic_tension:0.2
mesh_pps: 4, 4

#####################################################################
# Probe
#####################################################################
[probe]
pin: ^!MKS_THR:gpio21
x_offset: 28
y_offset: 4.4
#z_offset: 1.549
speed: 5
samples: 3
samples_result: average
sample_retract_dist: 3
samples_tolerance: 0.08
samples_tolerance_retries:3

#####################################################################
# Heated chamber
#####################################################################
[heater_generic chamber]
heater_pin:PB10
max_power:1.0
sensor_type:NTC 100K MGB18-104F39050L32
sensor_pin:PA1
control: pid
# max_delta: 0.5
min_temp:-100
max_temp:70
pid_Kp: 62.872
pid_Ki: 0.165
pid_Kd: 5986.173
# pid_Kp:63.418 
# pid_Ki:1.342 
# pid_Kd:749.125

[verify_heater chamber]
max_error: 300
check_gain_time:480
hysteresis: 3
heating_gain: 1


########################################
# Filament runout sensor
########################################
[filament_switch_sensor filament]
pause_on_runout: False
runout_gcode:
            PAUSE
            SET_FILAMENT_SENSOR SENSOR=filament ENABLE=1
event_delay: 3.0
pause_delay: 0.5
switch_pin: !PC1


#####################################################################
# Fans
#####################################################################
## Mainboard cooling fan
[heater_fan borad_fan]
pin:PC4
max_power: 1.0
kick_start_time: 0.5
heater: extruder
heater_temp: 50.0
fan_speed: 1.0
off_below: 0

## Part cooling fan 
[output_pin partfan]
pin: MKS_THR:gpio2
pwm: True
cycle_time: 0.0100
hardware_pwm: false
value: 0
scale: 255
shutdown_value: 0.0

## Big side radial turbo fan
[output_pin sidefan]
pin: PA8
pwm: True
cycle_time: 0.0100
hardware_pwm: false
value: 0.00
scale: 255
shutdown_value: 0.0

## Activated charcoal blowing fan
[output_pin filterfan]
pin:PC9
pwm: True
cycle_time: 0.0100
hardware_pwm: false
value: 0.0
scale: 255
shutdown_value: 0.0

## Cold end  and toolhead housing fans
[heater_fan hotend_fan]
pin:MKS_THR:gpio1
max_power: 1.0
kick_start_time: 0.5
heater: extruder
heater_temp: 50.0
fan_speed: 1.0
off_below: 0

[heater_fan hotend_fan2]
pin:MKS_THR:gpio20
max_power: 1.0
kick_start_time: 0.5
heater: extruder
heater_temp: 50.0
fan_speed: 1.0
off_below: 0


#####################################################################
# Light
#####################################################################
## caselight LEDs
[output_pin caselight]
pin: PC7
pwm: false
shutdown_value:0
value:1


#####################################################################
# Buzzer
#####################################################################
## Buzzer
[output_pin buzzer]
pin: PA2
pwm: false
shutdown_value:0
value:0

[output_pin sound]
pin: PA13
value:0

#####################################################################
# Power outage shutdown
#####################################################################
[output_pin pwc]
pin: PA3
pwm: False
value: 1
shutdown_value: 1
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

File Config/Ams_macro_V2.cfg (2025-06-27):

###############################################################################
##  General Config and overall variables
###############################################################################


### Todo:
    ## Test unloading and then loading part again and again (tweak lenghts)      ----------Needs to load, test coordination gathering (done)
    ## Get Flushing and cleaning X and Y Coordinates, [UNLOAD_AND_CUT_FILAMENT]      --------In the back a bit to left from the middle (mostly)
    ## Edit the tool change loading Part, the corrdinates, to much travel (done)
    ## Homing for feeders, to get accurate loading distance (not active just loading ,bc all from loqading to active will stay the same (530mm))  (hard to do, so probs no)
    ## Edit active calculations, use the final lenght already so no calculations are needed (done)
    ## Rethink unload_and_cut travels and such (mostly, wipe still needed)
    ## Edit start print gcode, for loop so even if i have more than 4 feeders i dont need to edit more if statements (done)

    ## Cute and clean, wait a bit before going to 


[save_variables]
filename: variables.cfg


###############################################################################
##  Enhanced Console Output Configuration
###############################################################################

# Enable RESPOND command and M118 for enhanced console output
# This replaces M118 commands with console-friendly alternatives that support:
# - Multi-line text display in Mainsail/Fluidd console
# - Better message categorization (info, error, warning)
# - Improved readability in terminal output
[respond]
default_type: echo
#   Sets the default prefix of the "M118" and "RESPOND" output to one
#   of the following:
#       echo: "echo: " (This is the default)
#       command: "// "
#       error: "!! "
#default_prefix: echo:
#   Directly sets the default prefix. If present, this value will
#   override the "default_type".


###############################################################################
##  General macros 
###############################################################################


[gcode_macro CONFIG]
variable_loaded_distance9: 0
variable_loaded_distance0: 390
variable_loaded_distance1: 390
variable_loaded_distance2: 250
variable_loaded_distance3: 380

variable_unactive_distance9: 0
variable_unactive_distance0: 525
variable_unactive_distance1: 530
variable_unactive_distance2: 535
variable_unactive_distance3: 535

variable_active_distance9: 0
variable_active_distance0: 530
variable_active_distance1: 530
variable_active_distance2: 530
variable_active_distance3: 530

variable_unloaded_distance9: 0
variable_unloaded_distance0: 10
variable_unloaded_distance1: 10
variable_unloaded_distance2: 10
variable_unloaded_distance3: 10

variable_multiplier9: 0
variable_multiplier0: 1
variable_multiplier1: 1
variable_multiplier2: 1
variable_multiplier3: 1

variable_load_speed: 10
variable_feeders: 4

description: A gcode to load the config values
gcode:
    M118 Global Config Loaded... Active Distance: {active_distance0} Feeders: {feeders} GLOBAL_CONFIG: {CONFIG}

[gcode_macro RESET_VARIABLES]
description: Resets all saved variables in variables.cfg, and if a feeder is loaded will unload it
gcode:
    {% set svv = printer.save_variables.variables %}
    
    {% set feeders = printer["gcode_macro CONFIG"].feeders %}
    {% set load_speed = printer["gcode_macro CONFIG"].load_speed %}

    {% for n in range(feeders) %}
        {% set active = svv['active' ~ n|string]|default(0)|int %}
        {% set loaded = svv['loaded' ~ n|string]|default(0)|int %}

        # Retrieve feeder-specific distances
        {% set active_distance = printer["gcode_macro CONFIG"]['active_distance' ~ n|string] %}
        {% set loaded_distance = printer["gcode_macro CONFIG"]['loaded_distance' ~ n|string] %}
        {% set unloaded_distance = printer["gcode_macro CONFIG"]['unloaded_distance' ~ n|string] %}
        {% set multiplier = printer["gcode_macro CONFIG"]['multiplier' ~ n|string] %}

        # Unload if active but not loaded
        {% if active != 0 and loaded == 0 %}
            M118 Resetting active Feeder {n}
            UNLOAD_AND_CUT_FILAMENT EXTRUDER={n}
            SET_GCODE_OFFSET Z_ADJUST=0
            SYNC_EXTRUDER_MOTION EXTRUDER=feeder_{n} MOTION_QUEUE=
            FORCE_MOVE STEPPER="extruder_stepper feeder_{n}" DISTANCE={multiplier * -active_distance} VELOCITY={load_speed}
            SET_STEPPER_ENABLE STEPPER="extruder_stepper feeder_{n}" ENABLE=0
        {% endif %}

        # Reset if loaded but not active
        {% if loaded != 0 and active == 0 %}
            M118 Resetting loaded Feeder {n}
            SET_GCODE_OFFSET Z_ADJUST=0
            SYNC_EXTRUDER_MOTION EXTRUDER=feeder_{n} MOTION_QUEUE=
            FORCE_MOVE STEPPER="extruder_stepper feeder_{n}" DISTANCE={multiplier * -active_distance} VELOCITY={load_speed}
            SET_STEPPER_ENABLE STEPPER="extruder_stepper feeder_{n}" ENABLE=0
        {% endif %}

        # Reset if both loaded and active
        {% if loaded != 0 and active != 0 %}
            M118 Resetting active and loaded Feeder {n}
            UNLOAD_AND_CUT_FILAMENT EXTRUDER={n}
            SET_GCODE_OFFSET Z_ADJUST=0
            SYNC_EXTRUDER_MOTION EXTRUDER=feeder_{n} MOTION_QUEUE=
            FORCE_MOVE STEPPER="extruder_stepper feeder_{n}" DISTANCE={multiplier * -active_distance} VELOCITY={load_speed}
            SET_STEPPER_ENABLE STEPPER="extruder_stepper feeder_{n}" ENABLE=0
        {% endif %}

        SAVE_VARIABLE VARIABLE=active{n} VALUE=0
        SAVE_VARIABLE VARIABLE=loaded{n} VALUE=0
    {% endfor %}

    SAVE_VARIABLE VARIABLE=last_feeder VALUE=9

    M118 All feeders reset!



[gcode_macro CHECK_RESETS]
description: This gcode checks if the variables.cfg file has already been generated, if not then it calls the RESET_VARIBBABLES macro
gcode:
    {% set svv = printer.save_variables.variables %}

    # Check if 'used' exists in saved variables
    {% if 'used' not in svv %}
        # Variable 'used' is not defined, initialize it
        RESET_VARIABLES
        SAVE_VARIABLE VARIABLE=used VALUE=1
    {% else %}
        # Variable 'used' exists, increment its value
        {% set used = svv.used|int %}  # Ensure 'used' is treated as an integer
        SAVE_VARIABLE VARIABLE=used VALUE={used + 1}
    {% endif %}


###############################################################################
##  Replacement for existing macros
###############################################################################


[gcode_macro PRINT_START]
description: Start printing
gcode:
    CLEAR_PAUSE

    # Ensure all axes are homed
    # G28 ; Home all axes

    # Clear any existing bed mesh and create a new one
    BED_MESH_CLEAR

    {% set svv = printer.save_variables.variables %}
    {% set feeders = printer["gcode_macro CONFIG"].feeders %}
    {% set last_feeder = svv.last_feeder %}

    {% set active = 9 %}

    {% for n in range(feeders) %}
        {% set activen = svv['active' ~ n|string]|default(0)|int %}
        {% if activen == 1 %}
            {% set active = n %}
            SET_STEPPER_ENABLE STEPPER="extruder_stepper feeder_{active}" ENABLE=1
            SYNC_EXTRUDER_MOTION EXTRUDER=feeder_{active} MOTION_QUEUE=extruder
            # SAVE_VARIABLE VARIABLE=last_feeder VALUE={active}
        {% else %}
            SYNC_EXTRUDER_MOTION EXTRUDER=feeder_{n} MOTION_QUEUE=
            SET_STEPPER_ENABLE STEPPER="extruder_stepper feeder_{n}" ENABLE=0
        {% endif %}
    {% endfor %}

    {% if last_feeder == 9 %}
        M117 Error: No active feeder!
        T0
    {% endif %}
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

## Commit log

2025-01-27 Stl files
    Added all necessary stl files, with if they are remixed or coppied, the original link/author.
    [Back_Spool_Holder_Adapter.stl, Bucket_Filament.stl, Filament_cutter.stl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]
2025-06-11 Added conf and macros
    It adds the necessary config files for this setup and the macros created to run this
    [Ams_macro_V2.cfg, Ams_v2.cfg, Filament_cutter.stl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]
2025-06-11 Updated Installation guide
    [Cutter_Stop.stl]
2025-06-27 Shortened Macros
    [Ams_macro_V2.cfg, printer.cfg]
